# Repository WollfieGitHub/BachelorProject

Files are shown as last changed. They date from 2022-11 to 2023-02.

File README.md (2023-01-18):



# BachelorProject - MDF/Stepper OpenSource Robotic Arm

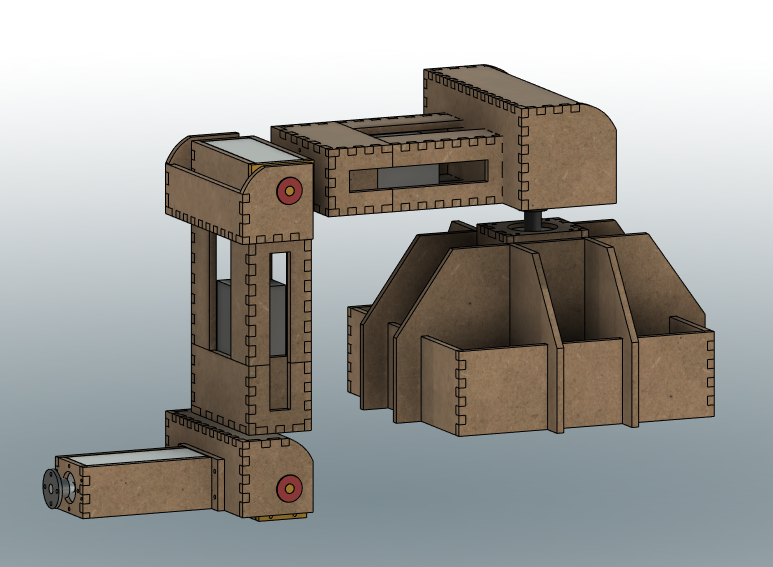
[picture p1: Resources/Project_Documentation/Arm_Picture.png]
Image of the robotic arm in fusion 360 Robotic Arm


## Table of Content

1. [Building Prerequisites](#building-prerequisites) : Material and electronic components needed to build the arm
   1. [Electronics](#electronics)
   2. [Mechanical Pieces](#mechanical-pieces)
   3. [Raw Material](#raw-material)
2. [Assembly Instructions](#assembly-instructions) : Step-by-step instructions to build the arm
3. [Control Software](#control-software--cottus-arm-controller) : Download instructions for a basic software to control the arm
   1. [Download Instructions](#download-instructions) : Download instructions
   2. [Code Architecture Documentation](#developer-instructions): General description of the software's architecture
      1. [Server](#server) : The server side of the software
      2. [Client](#client) : The client side of the software
4. [Future Work](#future-work-) : Possible improvements
5. [Scholar Papers](#scholar-papers): The scholar papers that were useful to this project

## Building Prerequisites

### Electronics

#### Raspberry Pi
- user: `cottus-pi`
- pass: `cottus-pi-s3cur3`

### Mechanical Pieces

#### 3D Printing

Pieces that should be 3D printed can be found as `.stl` files in the [Prints](./Prints) directory

#### Laser Cutting

Pieces that should be laser cut can be found as `.dxf` files in the [Prints](./Prints) directory.
6mm thick MDF should be used for all laser cut parts. They are named according to the referential of 
the arm's model in Fusion360

#### Screws
- [x16] : M4*12mm > Nema 17 Stepper Upper connection
- [x12] : M3*20mm > Nema 17 to Gearbox Adapter Connection
  - You might not need these
- 

### Raw Material

- [x3] : Aluminium/Metallic axle : 8mm in diameter
- [x1] : Wood glue stick for MDF assembly

## Assembly Instructions

The Fusion 360 file of the entire arm that you can import can be found [here](./Resources/Robotic%20Arm%20v110.step). It
contains all the 3D pieces and sketches resulting in the `.stl` and `.dxf` files you can find in the [Prints](./Prints) directory

## Control Software : Cottus Arm Controller

### Download Instructions

### Developer Instructions

#### General Architecture
The arm's controller hosts a server which the software's web client connects to in order to control it.
The server opens a serial connection on startup to communicate to the Arduino Mega via predefined packets :
- From PI to Arduino : Target angles (In degrees)
- From Arduino to PI : Motor speed (At startup, in deg/sec) and Current angles position (In loop, in degrees)

#### Server

##### Framework used :
The framework chosen to code the backend of the application is **Quarkus**. It is a recent
framework resembling Spring Boot. It has a well documented API that I invite you to [check
here](https://quarkus.io/). 

Several libraries act on top of this layer :
- [jSerialComm](https://github.com/Fazecast/jSerialComm) : Communicates with the Arduino Mega using the Serial connection
- [Efficient Java Matrix Library (ejml)](https://github.com/lessthanoptimal/ejml) : Matrix multiplications and other operations
- Quarkus-based :
  - [Rest-easy-Reactive-Jackson](https://quarkus.io/guides/rest-json) : Serialization of objects and [Reactive](https://quarkus.io/guides/getting-started-reactive) endpoints
  - [Websocket](https://quarkus.io/guides/websockets) : Communication with client using websockets
  - [Mongo DB with Panache](https://quarkus.io/guides/mongodb-panache) : Stores objects (animations) in Mongo Database with the Panache abstraction layer 

[Docker Compose](https://docs.docker.com/compose/) is used to set up the services of this project (server and database)
using the [docker-compose.yml file](./Software/cottus-controller/docker-compose.yml).

Docker-compose can be installed on Windows
easily with [Chocolatey](https://docs.chocolatey.org/en-us/choco/setup), adding the `C:\ProgramData\chocolatey\lib` path to the `Path` System
environment variable.

#### Architecture :
```
src/java/packagename/
   ⎿ dto
   ⎿ exception
   ⎿ models
   ⎿ repositories
   ⎿ resources
   ⎿ security
   ⎿ services
   ⎿ utils
```
##### dto
Objects sent by Quarkus as a response to an HTTP request are serialized by the 
Jackson library. They are decomposed into basic types to the JSON format. 
In order to facilitate this process and agree with the frontend to a common representation
of the objects travelling over the network, we use the DTO (Data Transfer Objects) layer.

As such, each object is re-declared in this layer and made serializable for the Jackson
library. The exact same definition of the DTOs can be found on the frontend's side. 
Only fields interesting to the other side of the network should be specified on this layer,
as the rest of them are not relevant and may often constitute abstraction leaks.

##### exception
This directory holds all the custom exceptions for the application

##### models
This is the only directory (along with `utils` to some extent) that should hold the implementation
details of the model behind your application (also referred as "business logic"). 

In our case, it holds all the computation for the control of the arm. 

##### repositories

Repositories used for persisting objects in the application. In our case, we have
a Mongo service running in a docker container

For now, only animations are saved to the database

##### resources
The `resources` directory declares all the endpoints reachable by the frontend. Handling
of all types of HTTP requests (`GET`, `POST`, ...) is implemented here even though it can
be mostly summed up to forwarding the calls to the `services` layer.

##### security
This directory handles the security logic of the application, which currently isn't much.

For now, it simply checks that a client trying to establish a connection to websocket does
so with a valid token that it previously got from an HTTP request to the server.

##### utils
Everything that isn't really proper to the business logic goes here. That includes
things like implementation of mathematical concepts like Vector3D...

##### Dependency Graph
Dependency Graph of the Server's Beans

#### Client

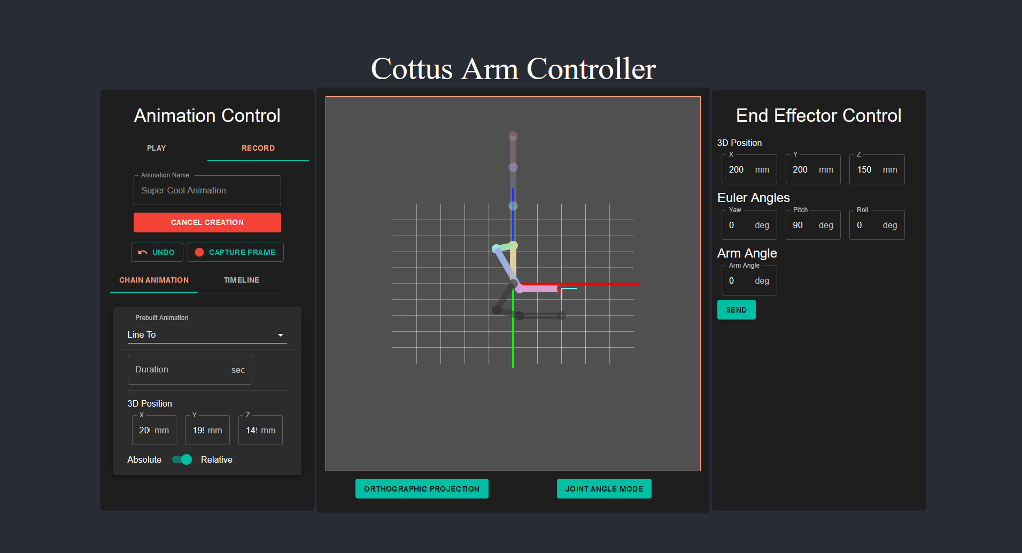
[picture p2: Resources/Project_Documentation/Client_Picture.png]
Picture of the Arm Controller Frontend page


##### Framework used :
The framework chosen to code the frontend of the application
is [React](https://reactjs.org/) with a layer of [TypeScript](https://www.typescriptlang.org/)
on top to enforce types and have a cleaner code with improved auto-completion from the IDE.

The React code also uses the [Material UI](https://mui.com/material-ui/getting-started/overview/)
library to have nice-looking components out of the box.

##### Architecture :
A description of the principles of the architecture used can be found [here](https://paulallies.medium.com/clean-architecture-typescript-and-react-8e509098abfe)

## Future Work:

Sources of imprecision
1. The metal pieces' insert connecting the motor's axle to the rest of the structure
tend to untighten
2. The PETG printed piece under the joint labelled `Shoulder_1` bends under the weight
of the arm

Other remaks :
1. The motors must be very slow when acting with an extended arm due to the high torque

## Scholar Papers:
Papers that I read fully or just in diagonal in the format (Only most relevant papers read are listed here) :
`<Relevance/How much it was used>/5 - Name : [Desciption/Note]`

- `3/5` - [Design and Implementation of a 6-DOF Intelligent Single-arm](Resources/Papers/25883917.pdf) : Learn the existence of Denavite-Hartenberg parameters and tables
- `5/5` - [Solution of Inverse Kinematics for 6R Robot Manipulators With Offset Wrist Based on Geometric Algebra](Resources/Papers/jmr_005_03_031010.pdf)
- `3/5` - [Introduction to Inverse Kinematics](Resources/Papers/iksurvey.pdf) : List of different methods for 
solving inverse kinematics numerically
- `5/5` - [Analytical Inverse Kinematic Computation for
  7-DOF Redundant Manipulators With Joint Limits
  and Its Application to Redundancy Resolution](Resources/Papers/Analytical_Inverse_Kinematic_Computation_for_7-DOF_Redundant_Manipulators_With_Joint_Limits_and_Its_Application_to_Redundancy_Resolution.pdf)
: Complete solution for analytical Inverse Kinematics
- `4/5` - [An Analytical Solution for Inverse Kinematics of
  7-DOF Redundant Manipulators with Offsets at
  Elbow and Wrist](Resources/Papers/An_Analytical_Solution_to_Inverse_Kinematics_of_Seven_Degree-of-freedom_Redundant_Manipulator.pdf) : Helped 
understand the previous paper

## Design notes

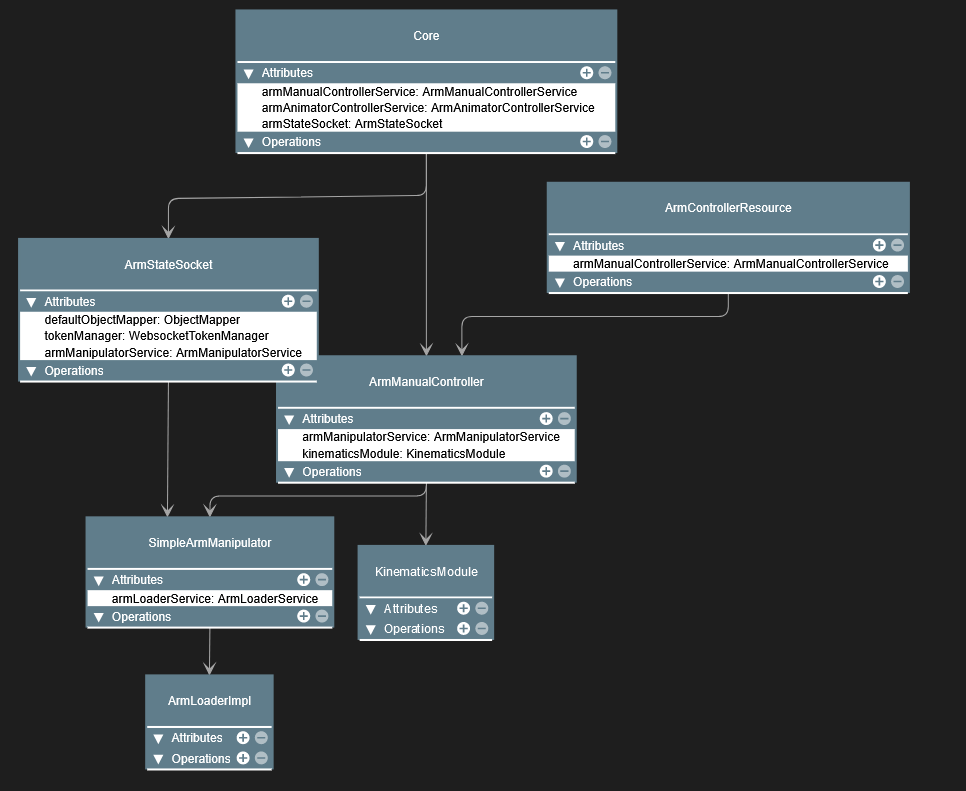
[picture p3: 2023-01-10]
Resources/Project_Documentation/Service Diagram.png

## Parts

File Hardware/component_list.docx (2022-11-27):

# Component List

# Bachelor Project – Leo Wolff

## Mechanical Parts

2x Coupling Flange – 14mm

5x Coupling Flange – 8mm

## Electronics

7x Limit switches

28x Screws (4mm Diameter, between 12 and 18mm long)

28x Screws (3.5mm Diameter, 12mm long)

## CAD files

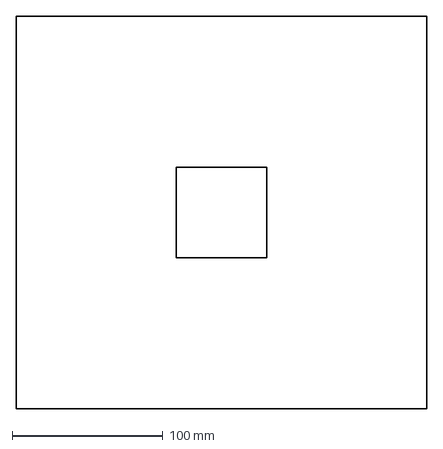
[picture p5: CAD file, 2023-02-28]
Prints/0_Base/Neg_Z.dxf
272.0 x 260.0 mm

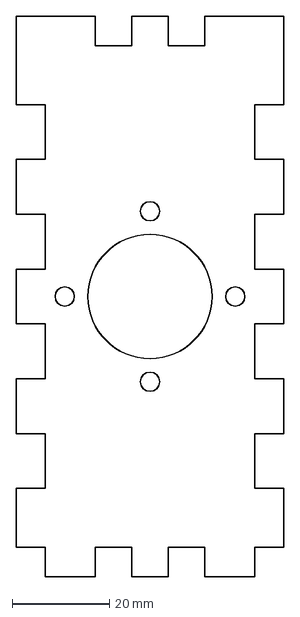
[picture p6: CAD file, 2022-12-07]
Prints/1_Elbow/A_0/Pos_Z.dxf
55.0 x 115.0 mm

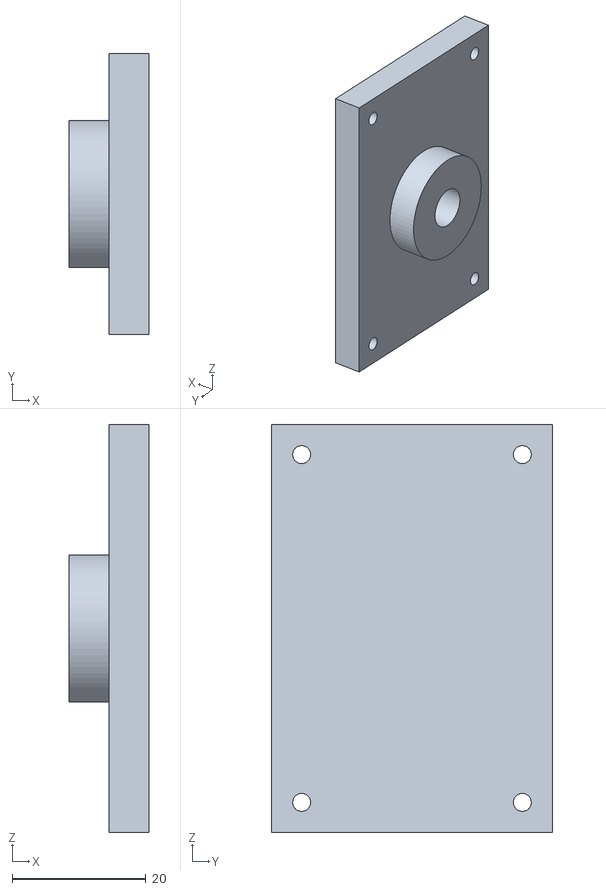
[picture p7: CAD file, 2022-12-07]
Prints/1_Elbow/A_1/A1_Pos_Y.stl
12.0 x 42.0 x 61.0

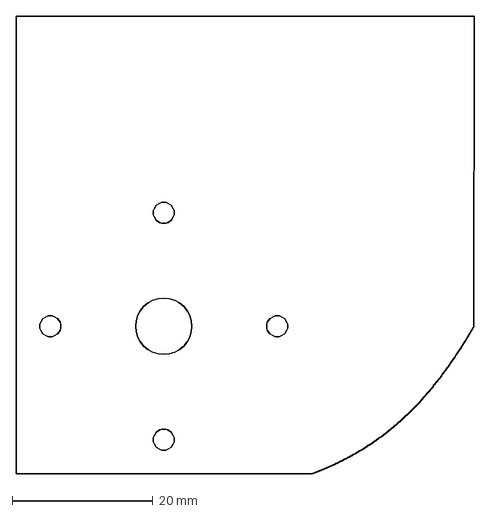
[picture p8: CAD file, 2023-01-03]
Prints/1_Elbow/A_2/Elbow_A2_Pos_Y_2.dxf
65.1 x 65.1 mm

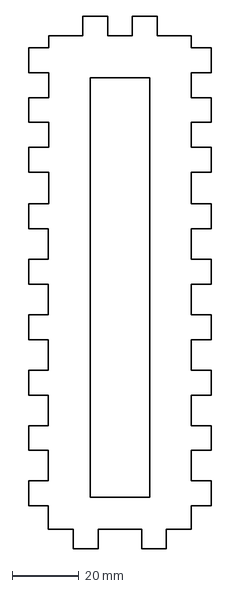
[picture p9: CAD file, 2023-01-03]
Prints/2_Wrist/A_0/Wrist_A0_Neg_Y.dxf
55.0 x 160.3 mm

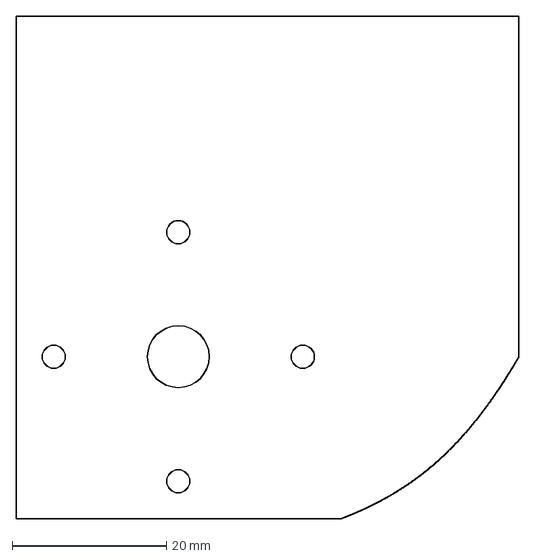
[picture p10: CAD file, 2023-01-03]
Prints/2_Wrist/A_2/Wrist_A2_Pos_Y_2.dxf
65.1 x 65.1 mm

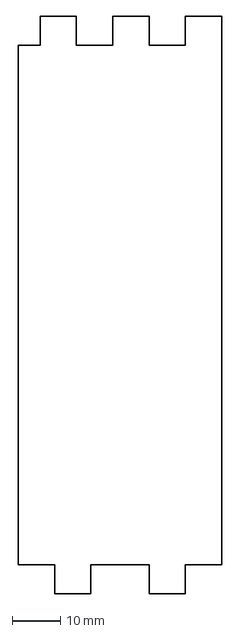
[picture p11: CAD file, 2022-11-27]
Prints/3_Hand/Hand_Pos_Y.dxf
42.0 x 119.5 mm

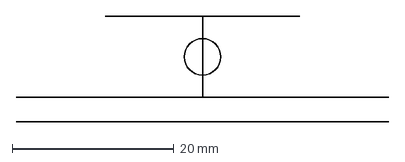
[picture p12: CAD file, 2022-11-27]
Prints/Coupling_Flange/coupling_flange_Nema23_sideview.dxf
46.0 x 13.0 mm

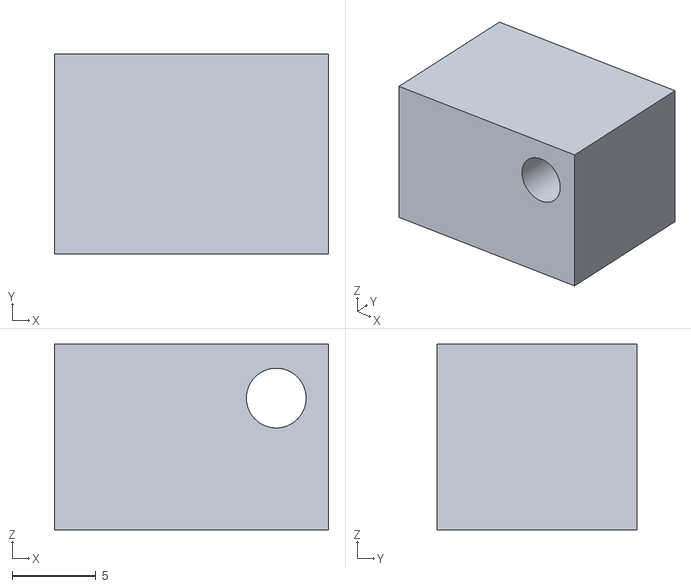
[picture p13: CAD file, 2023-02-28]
Prints/LimitSwitch_Holders/SwitchHolder_Wrist_0.stl
16.4 x 12.0 x 11.1

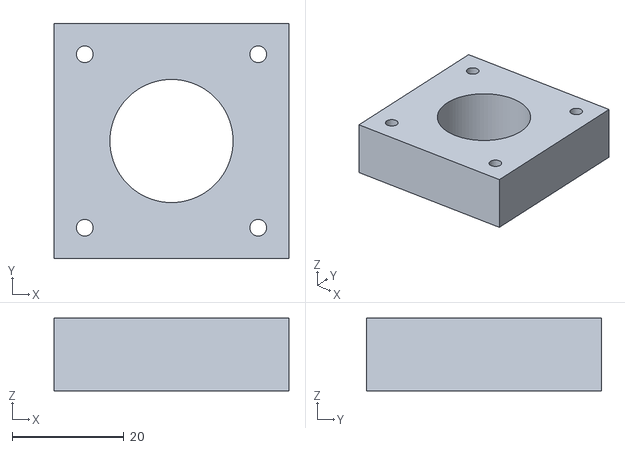
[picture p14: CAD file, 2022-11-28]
Prints/Motor_Gearbox_Joint/Nema17_Stepper_Gearbox_Joint.stl
42.0 x 42.0 x 13.0

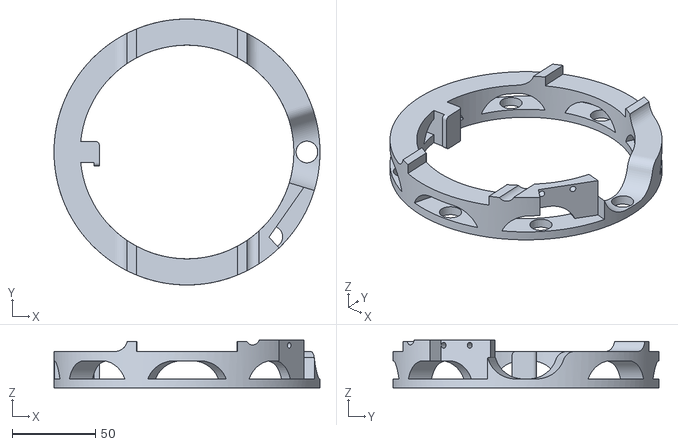
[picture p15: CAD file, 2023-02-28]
Prints/Turntable.stl
160.0 x 160.0 x 28.7

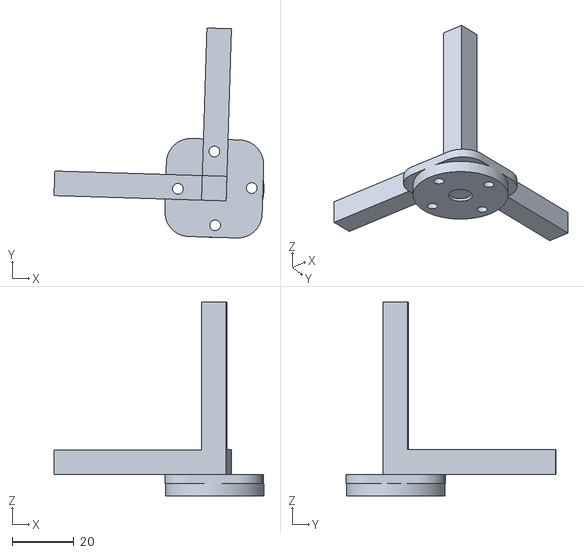
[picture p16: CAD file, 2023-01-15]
Prints/Utils/AxesIndicator.stl
68.3 x 68.3 x 63.0

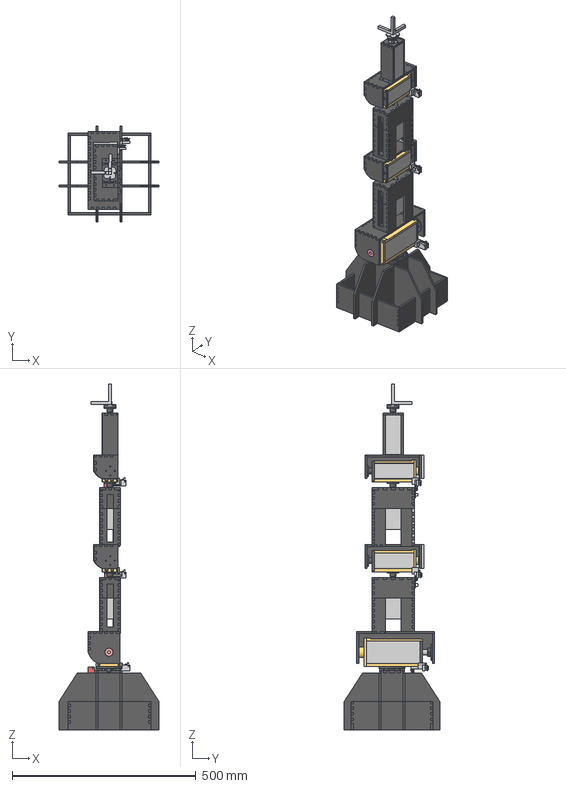
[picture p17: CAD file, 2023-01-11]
Resources/Robotic Arm v110.step
272.0 x 260.0 x 941.1 mm
Actuator17_4.2_20 x 5
PosYSide x 2
Core x 2
NegYSide (1) x 2
NegXSide (1) x 2
PosXSide (1) x 2
Bearing x 3
CouplingFlange8 x 5
PosXSide x 2
PosZSide x 2
NegXSide x 2
NegYSide x 2
PosX x 2
PosZ_1 x 2
NegZ x 2
Unused_1 x 2
A_1_Lid x 2
PosY
Unused
NegX_PosY
PosX_PosY
NegX_NegY
PosX_NegY
Unused (1)
HolderLid
PosZ
PosY_1
NegY
NegX_NegY (1)
PosX_NegY (1)
NegY (1)
PosY (1)
NegX_PosY (1)
PosX_PosY (1)
PosY_2
NegY_1
NegX
PosX_1
Actuator23_12.6_10
CouplingFlange14 x 2
PosY (2)
Unused (4)
Unused (5)
PosZ (1)
NegZ (1)
NegY (2)
RollingBearing x 6
NegX (1)
Unused (1)_1
PosX (1)
PosY (1)_1
NegY (1)_1
Switch x 6
Unused (2)
LimitSwitchHolder_Elbow
LimitSwitchHolderWrist
LimitSwitchHolderShoulder
BaseSwitchHolder
AxesIndicator

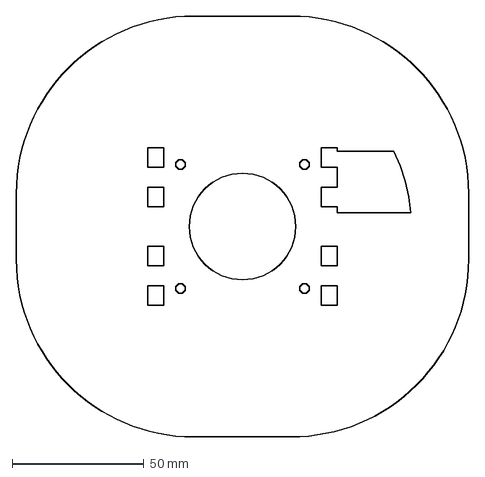
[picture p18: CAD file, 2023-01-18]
Prints/0_Base/Pos_Z.dxf
172.0 x 160.0 mm

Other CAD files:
Prints/1_Elbow/A_1/A1_Pos_Z.stl
Prints/1_Elbow/A_2/Elbow_A2_Pos_Y.dxf
Prints/2_Wrist/A_0/Wrist_A0_Pos_X.dxf
Prints/0_Base/A1_Neg_Y.stl
Prints/0_Base/A1_Neg_Z.dxf
Prints/0_Base/A1_Neg_Z.stl
Prints/0_Base/A1_Pos_X.dxf
Prints/0_Base/A1_Pos_Y.dxf
Prints/0_Base/A1_Pos_Z.dxf
Prints/0_Base/A1_Pos_Z.stl
Prints/0_Base/A2_Neg_X.dxf
Prints/0_Base/A2_Neg_Y.dxf
Prints/0_Base/A2_Pos_Y.dxf
Prints/0_Base/A2_Pos_Z.dxf
Prints/0_Base/Blocker.dxf
Prints/0_Base/Lid.dxf
Prints/0_Base/MotorLid.stl
Prints/0_Base/Neg_X.dxf
Prints/0_Base/Neg_Y.dxf
Prints/0_Base/Pos_X.dxf
Prints/0_Base/Pos_Y.dxf
Prints/0_Base/Ring_Neg_Y.dxf
Prints/0_Base/Ring_Neg_x.dxf
Prints/0_Base/Ring_Pos_X.dxf
Prints/0_Base/Ring_Pos_Y.dxf
Prints/0_Base/TurnTable.stl
Prints/1_Elbow/A_1/A1_Neg_Z.stl
Prints/1_Elbow/A_1/Elbow_A1_Neg_Y.dxf
Prints/1_Elbow/A_2/Elbow_A2_Neg_X.dxf
Prints/1_Elbow/A_2/Elbow_A2_Neg_Y.dxf
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

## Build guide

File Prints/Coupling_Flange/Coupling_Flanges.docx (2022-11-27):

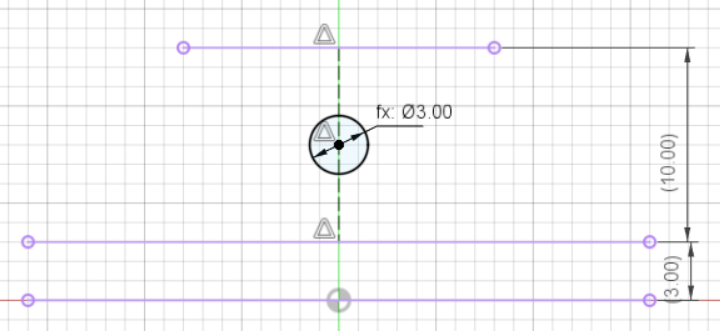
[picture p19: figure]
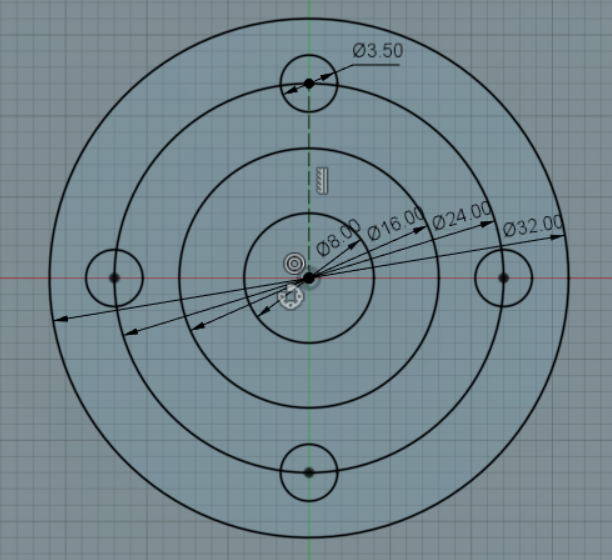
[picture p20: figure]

# x7

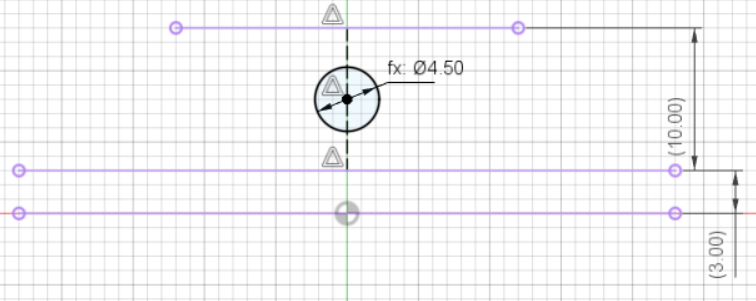
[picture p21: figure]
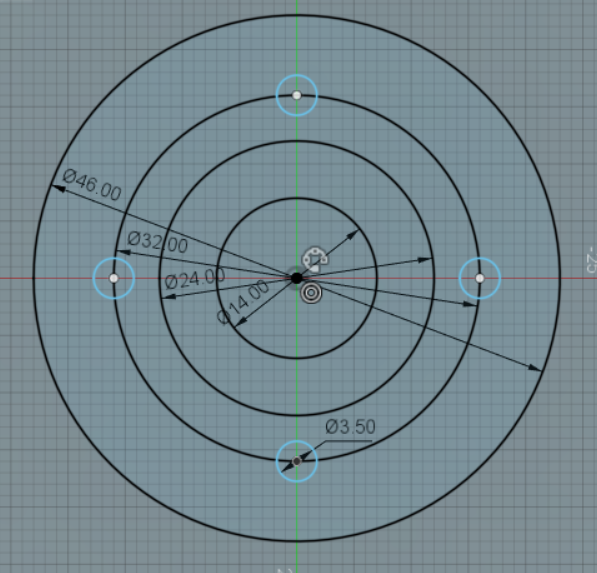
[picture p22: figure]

# x3

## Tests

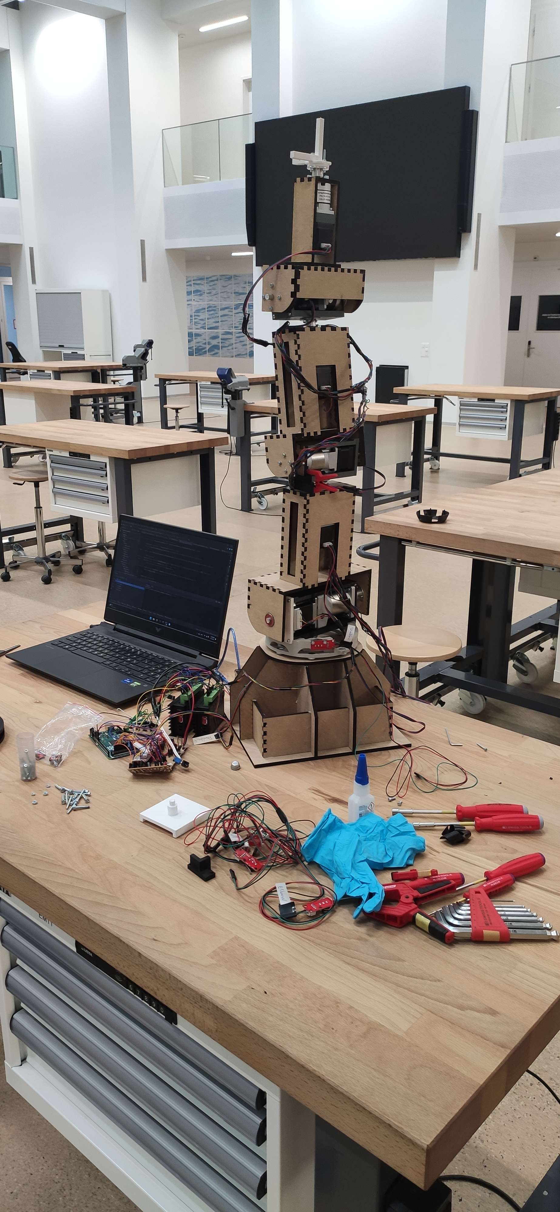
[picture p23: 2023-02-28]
ResultPictures/Picture_1.jpg

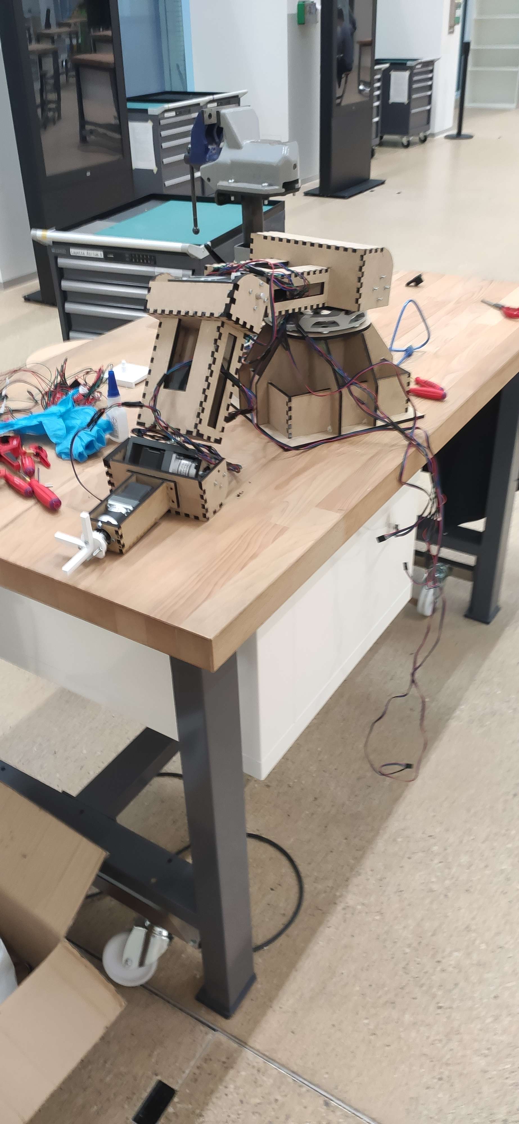
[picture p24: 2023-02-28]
ResultPictures/Picture_0.jpg

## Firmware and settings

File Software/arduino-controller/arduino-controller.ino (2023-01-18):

#include <AccelStepper.h>

#define MotorInterface 1
#define NB_STEPPERS 7
#define SWITCH_PRESS_STATE 0

#define MOTOR_SPEED 10
#define MOTOR_ACCEL 16

#define DISTANCES_END_VALUE_MARKER "D"

// TODO CHECK REDUCTIONS
const int pulsePins[] =          {   24,  28,  34,  38,  42,  46,  50 };
const int dirPins[] =            {   26,  30,  36,  40,  44,  48,  52 };

const int gearbox_reductions[] = {   10,  50,  10,  50,  10,  10,  10 };
const int micro_steps[] =        {    8,   8,   1,   1,   1,   1,   1 };
const double deg_per_step[] =       {  1.8, 1.8, 1.8, 1.8, 1.8, 1.8, 1.8 };
const int directions[] =         {    1,   1,   1,  1,   1,   1,   1 };

// TODO CHANGE
const double max_bound[] =         { 180.0, 90.0, 180.0, 90.0, 180.0, 90.0, 180.0};
const double min_bound[] =         { -180.0, -45.0, -180.0, -45.0, -180.0, -45.0, -180.0};

// positions (in steps) of the steppers
double positions[] =             {  0.0, 0.0, 0.0, 0.0, 0.0, 0.0, 0.0 }; // In degrees

const int limit_switch_pins[] =  {   2, 3, 4, 5, 6, 7, 8 };
const double limit_switch_pos[]= {  180.0,  45.0, 180.0,  45.0, 180.0,  45.0, 180.0 }; // Angle in degrees, must be converted to steps
const double homing_speed_factor[] = { 4.0, 0.25,  4.0,   0.25,  4.0,   0.25,  4.0 };
const double setup_dist_tolerance = 5 / 180.0 * PI; // The previous motor must be in a 5 Degrees tolerance distance of 0 before moving the next motor 


bool setup_failure = false;
int setup_index = 0;
bool is_setup_sequence_over = false;

// https://hackaday.io/project/183279-accelstepper-the-missing-manual/details
AccelStepper *steppers[] = { NULL, NULL, NULL, NULL, NULL, NULL, NULL };

String inputString = ""; // A string that holds the command sent by the server

void onDataReceived(String command);
String dataToSend();

long getSteps(int motorId, double deg);
double getAngleRad(int motorId, long steps);
double getDistance(int motorId);
void sendPositions();
void send_motor_speed();

void moveTo(int motorId, double angleRad);

bool isPressed(int switchPin);
void run_setup();

double to_radians(double degrees) {
    return degrees / 180.0 * PI;
}

double to_degrees(double rad) {
  return rad / PI * 180.0; 
}


void setup() {

    // Initialize Serial connection
    Serial.begin(9600);
    Serial.println("\nStarting setup...");

    // Initialize all steppers
    for (int i = 0; i < NB_STEPPERS; ++i) {
        steppers[i] = new AccelStepper(1, pulsePins[i], dirPins[i]);
        steppers[i]->setMaxSpeed(
          homing_speed_factor[i] * 
          MOTOR_SPEED * gearbox_reductions[i] * micro_steps[i]
        );    // So that all motors go to same speed
        steppers[i]->setAcceleration(MOTOR_ACCEL * gearbox_reductions[i] * micro_steps[i]); // So that all motors go to same speed

        // Set setup speed
        steppers[i]->setSpeed(
           homing_speed_factor[i] *
           directions[i]/4.0 * MOTOR_SPEED *
           gearbox_reductions[i] * micro_steps[i]
        );

        // Setup the limit switch's pin as an INPUT
        pinMode(limit_switch_pins[i], INPUT);
    }

    // Reserve 200 bytes
    inputString.reserve(200);

    Serial.print("Setup complete : ");
    Serial.println(setup_failure);

}

void loop() {

  if(setup_failure) { return; }

  if (!is_setup_sequence_over) { run_setup(); } 
  
  // Send positions anyway so that we can see the arm setup (Just for the sake of it)

}

void run_setup() {
  if(setup_index >= NB_STEPPERS) { // The last motor was setup
    is_setup_sequence_over = true;
    send_motor_speed(); // Send the motor speed, signaling to the server the arm can now receive commands
    return;

  } else if(setup_index > 0 && getDistance(setup_index-1) > getSteps(setup_index-1, setup_dist_tolerance)) { 
    return; // Wait for previous motor to reach 0 position
    
  } else if(isPressed(setup_index)) {
    // The steppers[setup_index] has reached the limit_switch
    // Stop the motor abruptly AND set its current position to its limit switch pos
    steppers[setup_index]->stop();
    steppers[setup_index]->setCurrentPosition(getSteps(setup_index, limit_switch_pos[setup_index]));
     // THIS ONLY WORKS CONSIDERING THAT THE ARM WITH ALL MOTORS TO 0 IS AN ARM POINTING TOWARDS THE CEILING
    steppers[setup_index]->moveTo(0);
    steppers[setup_index]->runToPosition(); 
    setup_index++;

  } else {
    // Move the stepper in the direction of its limit switch, one step by one step
    steppers[setup_index]->runSpeed();
  }
}

void moveTo(int motorId, double deg) {
    // Check that the motor is in bounds
    if ( min_bound[motorId] < deg && deg < max_bound[motorId] ) {
        steppers[motorId]->moveTo(getSteps(motorId, deg));
    }
}

void serialEvent() {
    if(!is_setup_sequence_over) { return; } // Do not accept messages when in setup mode

    while (Serial.available()) {
        // get the new byte:
        char inChar = (char)Serial.read();
        // add it to the inputString:
        inputString += inChar;
        // if the incoming character is a newline, call onDataReceived and clear the string
        // do something about it:
        if (inChar == '\n') {
            onDataReceived(inputString);
            inputString = "";
            break;
        }
    }
}

void onDataReceived(String command) {
    String msg = command;                              // Allocate a string for the message
    msg = msg.substring(0, 2);                         // Remove header

    int index = 0;
    for(int i = 0; i < NB_STEPPERS; i++) {             // For eachs Stepper :
      index = msg.indexOf(DISTANCES_END_VALUE_MARKER); //   Find next "D" marker
      String value = msg.substring(0, index);          //   Isolate the angle value
      moveTo(i, value.toDouble());                     //   Sets the target as the angle
      msg = msg.substring(index+1);                    //   Remove the value from the string
    }
}

String dataToSend() {
    // Send all angle positions
    String msg = "AN";
    for(int i = 0; i < NB_STEPPERS; i++) {
        msg += String(positions[i], 4) + DISTANCES_END_VALUE_MARKER;
    }

    return msg;
}

void send_motor_speed() {
  // Send the speed of the motor, also signals the server the arm did its setup sequence and is read to
  // receive instructions
  Serial.println("SP" + String(MOTOR_SPEED, 4));
}

double getDistance(int motorId) {
  return steppers[motorId]->distanceToGo();
}

void sendPositions() {
    for (int i = 0; i < NB_STEPPERS; i++) { positions[i] = getAngleDeg(i, steppers[i]->currentPosition()); } // Convert the positions in step to radians and store it
    Serial.println(dataToSend()); // Then send all the positions to the arm
}

long getSteps(int motorId, double deg) {
    return (gearbox_reductions[motorId] * micro_steps[motorId] * deg) / deg_per_step[motorId];
}

double getAngleDeg(int motorId, long steps) {
    return (steps * deg_per_step[motorId]) / (gearbox_reductions[motorId] * micro_steps[motorId]);
}

bool isPressed(int switchPin) {
  return digitalRead(limit_switch_pins[switchPin]) == SWITCH_PRESS_STATE;
}

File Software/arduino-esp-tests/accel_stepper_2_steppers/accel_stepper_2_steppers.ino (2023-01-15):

#include <AccelStepper.h>

#define m1Pulse  24     // Blue   - 28BYJ48 pin 1
#define m1Dir  26     // Pink   - 28BYJ48 pin 2
#define m1Reduc 50    // Motor Gearbox Reduction
#define m1MicStep 4   // Microstepping of the stepepr

#define m2Pulse  28     // Yellow - 28BYJ48 pin 3
#define m2Dir  30     // Orange - 28BYJ48 pin 
#define m2Reduc 10    // Motor Gearbox Reduction
#define m2MicStep 4   // Microstepping of the stepper

#define degPerStep 1.8 // Number of degrees in one step

#define MotorInterface 1
 
// Define two motor objects
// The sequence 1-3-2-4 is required for proper sequencing of 28BYJ48
AccelStepper stepper1(MotorInterface, m1Pulse, m1Dir);
AccelStepper stepper2(MotorInterface, m2Pulse, m2Dir);

void setup() {
  // put your setup code here, to run once:
  stepper1.setMaxSpeed(1000);
  stepper2.setMaxSpeed(1000);

  stepper1.setAcceleration(500);
  stepper2.setAcceleration(500);
}

void loop() {
  // put your main code here, to run repeatedly:

  moveTo(1, 90);
  delay(2000);
  moveTo(2, 90);
  delay(2000);
  moveTo(1, 0);
  delay(2000);
  moveTo(2, 0);
  delay(2000);
}

void moveTo(int mIndex, float deg) {
  if (mIndex == 1) {
    stepper1.moveTo(deg/degPerStep * m1Reduc * m1MicStep);
    stepper1.runToPosition();

  } else if (mIndex == 2) {
    stepper2.moveTo(deg/degPerStep * m2Reduc * m2MicStep);
    stepper2.runToPosition();
  }
}

void serialEvent() {

}

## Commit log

2022-11-28 Add print files and Screw Dimension image
    [A1_Neg_Y.stl, MotorLid.stl, Neg_Y.dwg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]
2022-11-28 Add beginning of screw specifications
2022-11-28 Did modification of screw holes
2022-12-07 Change to Readme, Initial commit of software
    [A1_Neg_Y.stl, A1_Neg_Z.dxf, A1_Neg_Z.stl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]
2022-12-09 Add description for scholar papers
    [A1_Neg_Z.stl, A1_Pos_Y.dxf, A1_Pos_Y.stl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]
2022-12-09 Add Paper on solving inverse kinematics for 6 DOF General Kinematic Chain
    [Elbow_A1_Neg_Y.dxf, Elbow_A2_Neg_X.dxf, Elbow_A2_Neg_Y.dxf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]
2023-01-03 Update Paper references
    [Elbow_A1_Neg_Y.dxf, Elbow_A2_Neg_X.dxf, Elbow_A2_Neg_Y.dxf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]
2023-01-03 Add missing files
    [Elbow_A2_Pos_Y_2.dxf, Wrist_A2_Pos_Y_2.dxf]
2023-01-09 Progress on arduino-controller.ino
2023-01-10 First version of finished arduino-controller.ino program
2023-01-11 Add Robotic Arm v110.step
    [Robotic Arm v110.step]
2023-01-15 Update README.md + Resources
    [AxesIndicator.stl, BaseSwitchHolder.stl, Elbow_A2_Neg_X.dxf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]
2023-02-28 Commit last changes to the on the model and switch holders
    [Neg_Z.dxf, Payment_records.xlsx, SwitchHolder_Shoulder_2.stl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]
